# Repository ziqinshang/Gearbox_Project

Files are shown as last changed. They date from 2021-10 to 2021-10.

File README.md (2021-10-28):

# Gearbox_Project
### This is a group project of a gear reduction system, The system consist of three shafts: Input, Intermediate and Output Shaft, Two pinions and two gears, all helical, with a gear reduction ratio of 1:16. The shafts are supported by appropriate bearings, A outer shell were also constructed for convering the inner components.
#### All the mathmatical calculations were performed using MATLAB
#### The prototype were modelled using Solidworks
#### Detailed engineering drawing were generated by Solidworks
#### Some hand-drawn graphs are available on design report
##### Group Effort
##### credit: Mingyang Xu, Maiduo Wu

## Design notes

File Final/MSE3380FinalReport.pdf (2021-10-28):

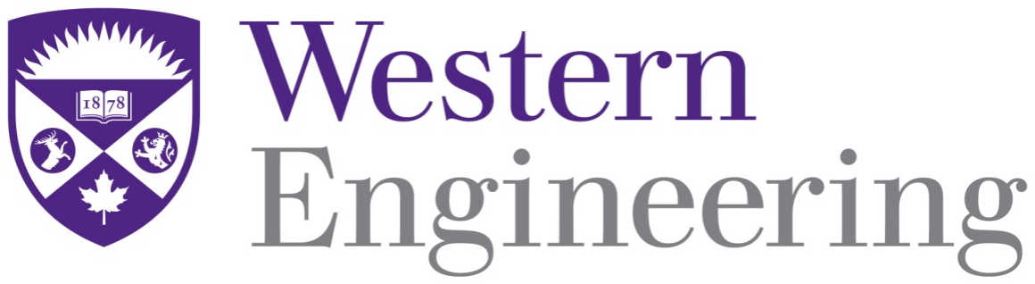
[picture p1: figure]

# MSE3380

## Mechanical Components Design for Mechatronic Systems Final Design Report

Group 5

Mingyang Xu (250902744)

Mai Duo Wu (250922745)

Ziqin Shang (250890594)

April 9th, 2019

Table of Contents

7. Bearing specification (manufacturer/model number) configuration and life calculation. Specify a

## Introduction

In the previous report, the gear specifications were determined, corresponding calculations

and CAD drawings were also completed. In this final report, the gearbox design will be

finalized, and results will be verified. a complete analysis of shaft and bearing, calculations

of shaft fatigue safety factor, shaft material endurance limit and bearing life will be

conducted.

## 1. Summary of The Analysis from The Phase 1 Report

Performance Specifications

In the interim report, the performance specification was firstly determined, including

the important specifications of weight, size and efficiency; constrains of gears, motor,

lifetime and output; and associated assumptions.

Gear Ratios and Reduction Stages

The gear ratio and reduction stages were specified, after a series of analysis including

DC motor no-load speed, DC motor stall torque and DC motor peak power, the required

torque output of DC motor was determined to be 3.717N.m, and the required speed output

was determined to be 9426rpm. Based on the calculated torque output, the gear ratio was

calculated to be 1:16.4, in order to implement this gear ratio, the two reduction stages were

determined to be 1:4 for both stages.

Torque Within the Shafts

The torque within the shaft was estimated, the shaft that connects to the DC motor will

experience least torque, which is the output of DC motor of 3.717N.m. And the

intermediate shaft will experience a torque of 14.105N.m, the final shaft will experience

most torque which is calculated to be 53.525N.m.

Forces on The Pinions and Gears and Their Dimensions

The forces on the pinions and gears and their dimensions was determined, the forces

between DC motor pinion and intermediate gear is calculated to be 2163.12N, the forces

between intermediate pinion and output gear is calculated to be 2052.14N. The gears were

carefully selected from the Boston gears catalog, the two pinions have the same dimensions

but different direction, with a transverse diametral pitch of 16 inch, 12 teeth, a pitch

diameter of 0.75 inch, a bore diameter of 0.375 inch, a keyway dimension of 1/16x1/32, A

style, and the catalog number is H1612R and H1612L respectively. The two gears also have

the same dimensions but different direction, with a transverse diametral pitch of 16 inch, 48

teeth, a pitch diameter of 3 inches, a bore diameter of 0.5 inch, a keyway dimension of

1/8x1/16, a style, and the catalog number is H1648R and H1648L respectively.

Contact and Bending Stress, Contact and Bending Safety for the Gears

The contact stress, bending stress, contact safety factor and bending safety factor of the

gears was calculated using MATLAB script, and the results is summarized below.

| Pinion 1 | Gear 2 | Pinion 3 | Gear 4
Bending Stress | 42209 | 40015 | 34607 | 33254
Contact Stress | 167743 | 94295 | 151888 | 85960

Bending FOS | 1.0 | 1.10 | 1.27 | 1.40
Contact FOS | 0.75 | 1.38 | 1.1 | 1.55

Additionally, the CAD model of the entire gearbox was completed, and the 2D assembly

drawing of the entire gearbox with cross-section was also drawn using Solidworks.

Updates

Due to fact that the calculated pinion 1 contact FOS is less than 1(Pinion 1 cannot

withstand such high pressure), all 4 gears’ transverse diametral pitch are changed to be 8 so

that the gear can withstand such a pressure and they can fit together without interference.

The specifications for newly updated gears can be found in appendix A.

## 2. Free Body Diagrams for Shafts

Included in Section 3: Calculation of All Torques and Forces Acting on Shafts

## 3. Calculation of All Torques and Forces Acting on Shafts

Firstly, the reaction forces in each shaft was determined, each shaft is supported by two

bearings that treated as a fixed support, since the helical gears are used, the forces between

the gear and pinion is three-dimensional, that is, force is acting on x, y and z axis. Detailed

calculations for reaction forces are demonstrated below.

Shaft 1 (Input Shaft):

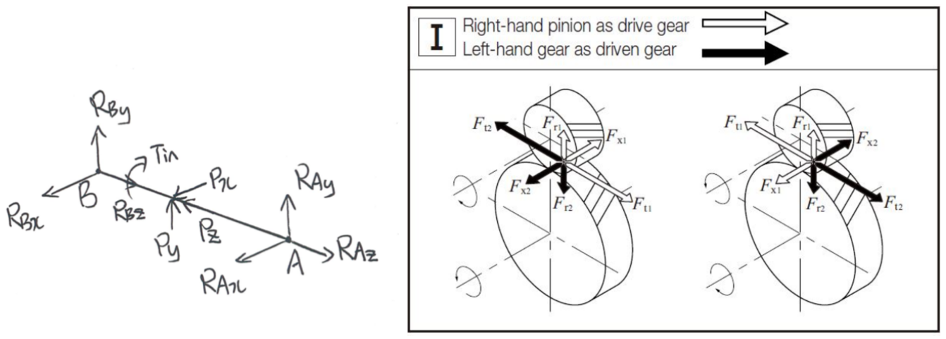
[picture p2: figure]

Figure 1. Free Body Diagram for input shaft

The forces between pinion 1 and gear 2 is calculated to be: P" = −W&'( = T

r = 14.105N. m
0.01905m = −740.42N

P5 = −W6'( = W&'( tanφ& = 740.42 ∗ tan 20.09 = −270.81N

P= = −W>'( = W&'( tan ψ = 740.42 ∗ tan 45 = −740.42N W = W&
cos ψ cosφC

= 740.42
cos 14.5 cos 45 = 1081.56N

From Free Body Diagram, the following equations can be listed:

ΣMG= = P=(1) + RL=(2) = 0

ΣMG5 = P5(1) + RL5(2) = 0

ΣF" = RL" + RG" − P" = 0 RG" = RL"(Assumption)

ΣF= = RL= + RG= + P= = 0

ΣF5 = RL5 + RG5 + P5 = 0

Solving equations above, the results are:

RL= = 370.21N | RL5 = 135.405N | RL" = −370.21N
RG= = 370.21N | RG5 = 135.405N | RG" = −370.21N

Shaft 2 (Intermediate Shaft):

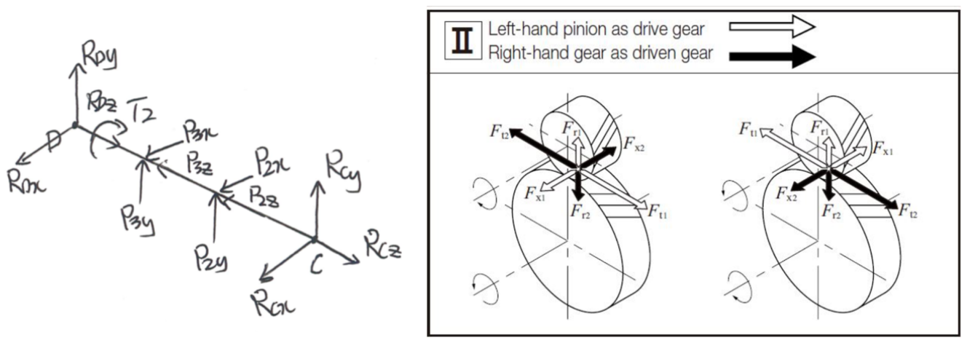
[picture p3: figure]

Figure 2. Free Body Diagram for intermediate shaft

The distance between point D and point 3 is determined to be 1/6 of the total shaft

length, distance between point 3 and shaft midpoint is determined to be 2/6 of the total

shaft length. The shaft is symmetrical.

The forces between pinion 3 and gear 4 and pinion 1 and gear 2 can be calculated based on

previous given formulas:

P(" = W&'( = P

6 = 'Q.'RST.U
R.R'VRSU = 740.42Ne

P(5 = W6'( = W&'( tanφ& = 740.42 ∗ tan 20.09 = 270.81N

P(= = W>'( = W&'( tan ψ = 740.42 ∗ tan 45 = 740.42N PW" = W&WQ = T

r = 53.525N. m
0.0762m = 702.43N

PW5 = W6WQ = W&WQ tanφ& = 1404.86 ∗ tan 20.09 = 256.9N

PW= = W>WQ = W&WQ tan ψ = 1404.86 ∗ tan 45 = 702.43N W = W&
cos ψ cosφC

= 702.43
cos 14.5 cos 45 = 1026.07N

From Free Body Diagram, the following equations can be listed:

ΣMX5 = PW5(1) + P(5(5) + RY5(6) = 0

ΣMX= = PW=(1) + P(=(5) + RY=(6) = 0

ΣF" = RX" + RY" + PW" − P(" = 0 RY" = RX"(Assumption)

ΣF5 = RY5 + RX5 + P(5 + PW5 = 0

ΣF= = RY= + RX= + P(=+ PW= = 0

Solving equations above, the results are:

RY= = −734.09N | RY5 = −268.492N | RY" = −19N
RX= = −708.76N | RX5 = −259.218N | RX" = −19N

Shaft 3 (Output Shaft):

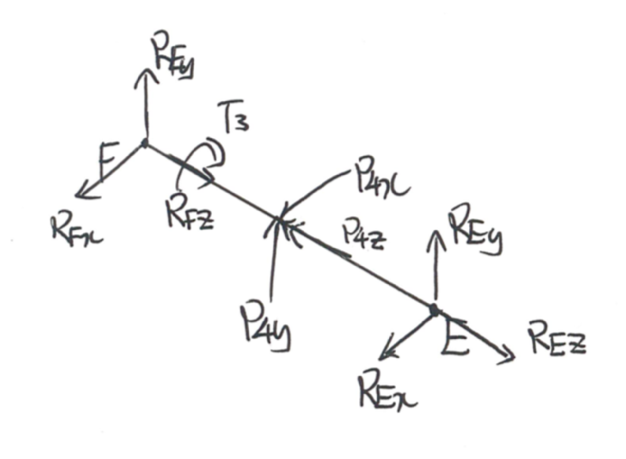
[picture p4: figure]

Figure 3. Free Body Diagram for output shaft The forces between pinion 3 and gear 4 can be calculated based on previous given formulas: PQ" = −W&WQ = T

r = 53.525N. m
0.0762m = −702.43N

PQ5 = −W6WQ = W&WQ tanφ& = 1404.86 ∗ tan 20.09 = −256.9N

PQ= = −W>WQ = W&WQ tan ψ = 1404.86 ∗ tan 45 = −702.43N

From Free Body Diagram, the following equations can be listed:

ΣMZ= = PQ=(1) + R[=(2) = 0

ΣMZ5 = PQ5(1) + R[5(2) = 0

ΣF" = RZ" + R[" − PQ" = 0 RZ" = R["(Assumption)

ΣF= = RZ= + R[= + PQ= = 0

ΣF5 = RZ5 + RZ5 + PQ5 = 0

Solving equations above, the results are:

R[= = 351.22N | R[5 = 128.46N | R[" = −351.22N
RZ= = 351.22N | RZ5 = 128.46N | RZ" = −351.22N

## 4. Shear, Moment and Torque Diagrams for Shafts

Pictures on next page.

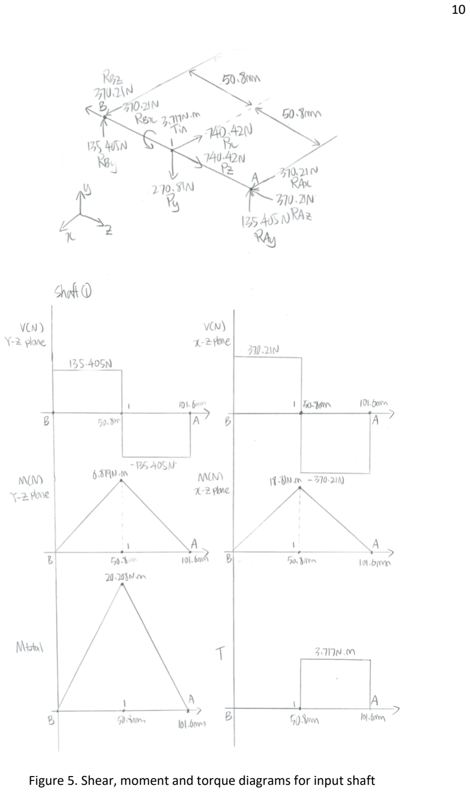
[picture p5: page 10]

Figure 5. Shear, moment and torque diagrams for input shaft

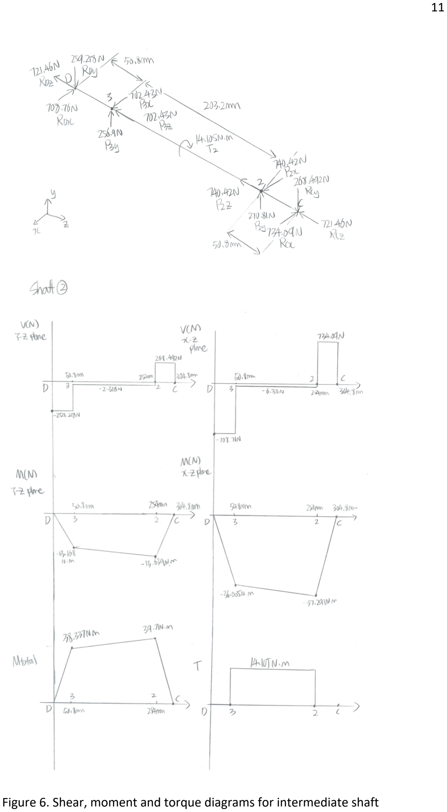
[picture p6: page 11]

Figure 6. Shear, moment and torque diagrams for intermediate shaft

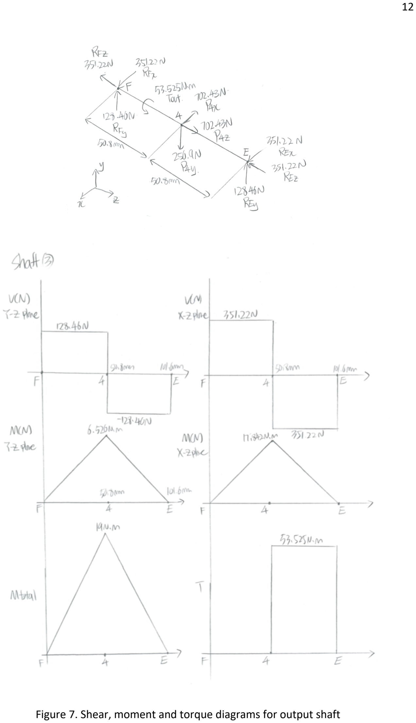
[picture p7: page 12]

Figure 7. Shear, moment and torque diagrams for output shaft

## 5. Fully Corrected Endurance Limit for Shaft Material

Include in Section 6. Shaft Fatigue Safety Factors

## 6. Shaft Fatigue Safety Factors

To obtain the endurance limit for shaft material, the shaft material needs to be determined,

the yield strength and tensile strength of the material needs to be sufficient in order to

prevent failure. In the case of transmission shaft, the material with high torsional rigidity

and fatigue resistance is preferred, which are steel and aluminum. Steel is extremely

durable, inexpensive, but heavy. On the other hand, aluminum is less durable but

significantly more lightweight than steel. In this application, lightweight is not a major

requirement, but high strength is preferred, as a result, steel is chosen for this application.

For initial test, AISI 1060 was implemented to calculate the endurance limit.

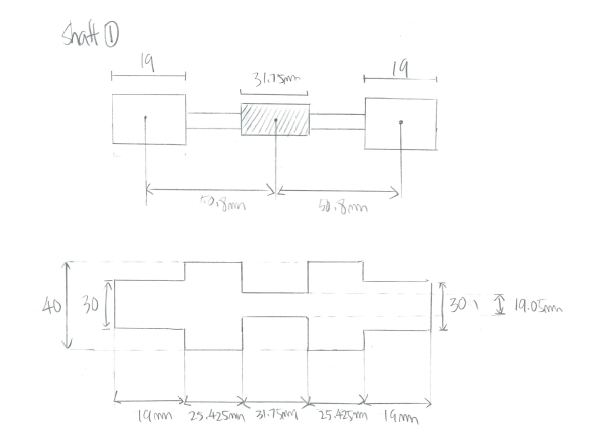
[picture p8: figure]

Figure 8. Dimensions for input shaft

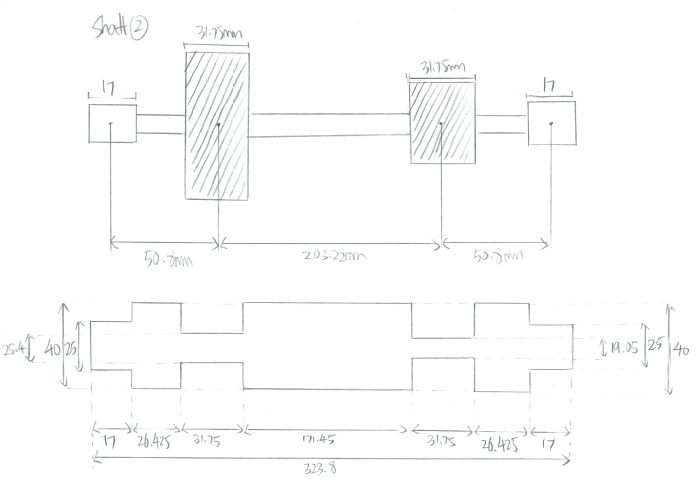
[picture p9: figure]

Figure 9. Dimensions for intermediate shaft

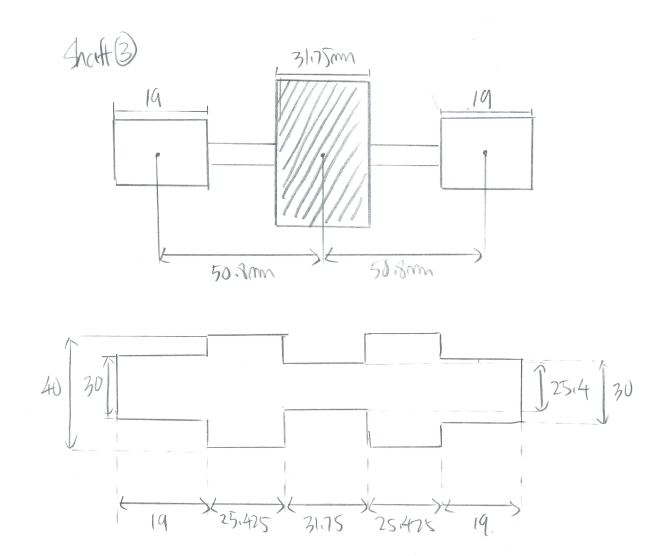
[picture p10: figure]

Figure 10. Dimensions for output shaft In order to determine endurance limit, the following analysis is performed.

1. The rotary-beam test specimen endurance limit of AISI is determined to be 340 MPa.

Using the equation

s]

^ = _

0.5Sa& Sa& ≤ 200kpsi (1400 MPa)
100 kpsi | Sa& > 200kpsi
700 MPa | Sa& > 1400 Mpa

As the Sut, the tensile strength of AISI 1060 is 680MPa, which is smaller than 1400 MPa,

the rotary-beam test specimen endurance is half of the tensile strength which is 340

MPa.

2. The corrected endurance limit at the critical location of a machine part in the

geometry and condition of use is given as:

S] = k>khkikjk]kkS]

^

The surface condition modification factor is given as k> = aSa&

h , where a and b are

found using the following table:

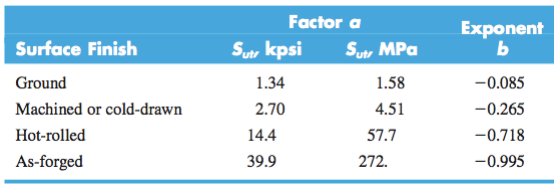
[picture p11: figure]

Solving the equation using the parameters of Machined or cold-drawn assuming the

shaft should be machined, ka = 0.8009.

3. The size factor is evaluated using the equations

The size factor is determined to be 0.9046 for shaft 1 and 2, and 0.8772 for shaft 3.

4. The Loading Factor Kc is determined to be 1 as the load factor is bending.
5. The temperature factor Kd is determined to be 1 as the electric drill should be used

in a room temperature condition.

6. The reliability factor, Ke was determined using the following table

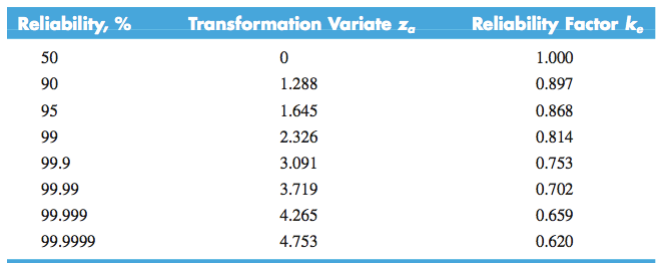
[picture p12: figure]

With 99% reliability, Ke was determined to be 0.814.

7. Miscellaneous-effects factor kf is assumed to be 1.

Then, fatigue stress-concentration factor is solved using the equation:

Kk = 1 +

K& − 1
1 + ma/r

Where Kt is the stress-concentration factor, a is the√a is the Neuber constant and r

is the fillet radius. Please see MATLAB files for calculations.

The stress is calculated using σ6]q = ri
s

.M is the moment derived from moment

diagram where stress concentration is located at the fillet transition location. c is the

radius of the smaller part of the shaft, and I is solved from I = ujv
wQ

. Refer to MATLAB for

calculations

The fatigue safety factors for shafts is solved as nk = Endurance limit Maximum reverseal stresses nk = S] Kkσ6]q

The results obtained are listed below:

| Se | Kf | srev | nf
Shaft 1 | 200.5MPa | 1.4811 | 26.04MPa | 5.20
Shaft 2 | 200.5MPa | 1.4811 | 58.17MPa | 2.33
Shaft 3 | 104.4MPa | 1.6077 | 24.5MPa | 4.93

All three shafts have a fatigue safety factors greater than 1 with a reliability of 99%. This

shows that the shafts should have an infinite life. This result is reasonable as the used

material for the shaft is steel which has a high tensile strength.

## 7. Bearing specification (manufacturer/model number) configuration

and life calculation. Specify a recommended lubrication strategy.

Firstly, the bearing type needs to be determined, in this application, helical gears were

used, as a result, there are thrust load and radial load exist. Bearings are manufactured to

take pure radial loads, pure thrust load or the combination of two, ball bearings are

considered to be the most suitable type for this application due to the fact that ball bearing

can withstand both thrust load and radial load in a considerable amount. Specifically, single-

row deep groove ball bearing was decided to be implement, since single-row deep groove

ball bearing is excellent for high-speed application, has good radial load capacity and

satisfactory thrust load capacity in both directions, and low torque capacity at start-up and

running speed. All bearings are selected from The Timken Company.

To further specify the bearing specification, the dynamic load and static load needs to

be determined, following procedures were used to determine these two values. Assuming:

- Continuous one-shift operation at 9426 rpm (8 hours day, 5-day week),

life=30kh

- Commercial gear, load factor = 1.2
- 90% reliability
- a=3 for ball bearing

Shaft 1:

Estimate life for 8-hour day:

LX = 9426rpm × 30kℎ ×

60m
ℎ = 1.6967 × 10'Rrev

The equivalent load:

F] = XÜVF6 + YÜF> , V = 1

Radial load = 394.2N Axial load = 370.12N

Since
F>

(VF6) = 370.21
394.2 = 0.939 > e eU>= = 0.44

Thus

F] = X((394.2) + Y((370.21)

First guess: X( = 0.56 Y( = 1.63

F] = 0.56(394.2) + 1.63(370.21) = 824.19N

Weibull parameters

xR = 0.02 θ = 4.459 b = 1.483

From Eq. (11–10):

C'R = 1.2(824.19) ç
é

1.6967 × 10'R
10w è

0.02 + (4.459 − 0.02)(1 − 0.90)

'

'.QêWë

'
W
= 25414.23N = 25.41kN

From T 11–2 (DG) bearing 02-40 mm has

C'R = 30.7kN CR = 16.6kN
F>
CR

= 0.0223, e ≈ 0.21, Y( = 2.15

F] = 0.56(394.2) + 2.15(370.21) = 1016.7N

C'R = 1.2(1016.7) ì

1.6967 × 10'R
10w î

'
W
= 31.35kN

From T 11–2 (DG) bearing 02-45 mm has

C'R = 33.2kN CR = 18.6kN
F>
CR

= 0.0199, e ≈ 0.2069, Y( = 2.1736

F] = 0.56(394.2) + 2.1736(370.21) = 1025.43N

C'R = 1.2(1025.43) ì

1.6967 × 10'R
10w î

'
W
= 31.62kN

Selecting from The Timken Company ball bearings catalog, two 30mm bore single-row deep

groove ball bearing will be used in both ends of input shaft. The bearing has a outside

diameter of 72mm, a width of 19mm, a fillet radius of 1.0mm, a weight of 0.354kg, a static

load rating of 15600N and an extended dynamic load rating of 33900N.

Bearing life:

ℒ'R = 60ℒñnñ
60nX

(

C'R
F]

)> = 10w
60(9426rpm)

## é ³³⁹⁰⁰

1025.43è

W
= 63885.5ℎ

Shaft 2:

Point C: Radial load = 781.65N Axial load = 19N F>

(VF6) = 19N
781.65N = 0.02431 < e eUÜC = 0.19

F] = 1(781.65) + 0(19) = 781.65N

C'R = 1.2(781.65) ì

1.6967 × 10'R
10w î

'
W
= 24.10kN

Point D: Radial load = 754.68N Axial load = 19N F>

(VF6) = 19N
754.68N = 0.02517 < e eUÜC = 0.19

F] = 1(754.68) + 0(19) = 754.68N

C'R = 1.2(754.68) ì

1.6967 × 10'R
10w î

'
W
= 23.27kN

Since the e is minimum for both bearings, no iteration needs to be performed, Selecting

from The Timken Company ball bearings catalog, two 25mm bore single-row deep groove

ball bearing will be used in point C and D of intermediate shaft. The bearing has a outside

diameter of 62mm, a width of 17mm, a fillet radius of 1.0mm, a weight of 0.236kg, a static

load rating of 12200N and an extended dynamic load rating of 26600N.

Bearing life at Point C:

ℒ'R = 60ℒñnñ
60nX

(

C'R
F]

)> = 10w
60(2356.5rpm)

é

26600
781.65è

W
= 278733.5ℎ

Bearing life at Point D:

ℒ'R = 60ℒñnñ
60nX

(

C'R
F]

)> = 10w
60(2356.5rpm)

é

26600
754.68è

W
= 309697.5ℎ

Shaft 3:

Radial load = 373.98N Axial load = 351.22N F>

(VF6) = 351.22N
373.98N = 0.939 > e eU>= = 0.44

F] = X((373.98) + Y((351.22)

First guess: X( = 0.56 Y( = 1.63

F] = 0.56(373.98) + 1.63(351.22) = 781.92N

Weibull parameters

xR = 0.02 θ = 4.459 b = 1.483

From Eq. (11–10):

C'R = 1.2(781.92) ì

1.6967 × 10'R
10w î

'
W
= 24.11kN

From T 11–2 (DG) bearing 02-35 mm has

C'R = 25.5kN CR = 13.7kN
F>
CR

= 0.0256, e ≈ 0.215, Y( = 2.07

F] = 0.56(373.98) + 2.07(351.22) = 936.45N

C'R = 1.2(936.45) ì

1.6967 × 10'R
10w î

'
W
= 28.88kN

From T 11–2 (DG) bearing 02-40 mm has

C'R = 30.7kN CR = 16.6kN
F>
CR

= 0.0212, e ≈ 0.21, Y( = 2.15

F] = 0.56(373.98) + 2.15(351.22) = 964.55N

C'R = 1.2(964.55) ì

1.6967 × 10'R
10w î

'
W
= 29.74kN

Selecting from The Timken Company ball bearings catalog, two 30mm bore single-row deep

groove ball bearing will be used in both ends of input shaft. The bearing has a outside

diameter of 72mm, a width of 19mm, a fillet radius of 1.0mm, a weight of 0.354kg, a static

load rating of 15600N and an extended dynamic load rating of 33900N.

Bearing life:

ℒ'R = 60ℒñnñ
60nX

(

C'R
F]

)> = 10w
60(589rpm)

é

33900
964.55è

W
= 1228452ℎ

For this application, oil is a preferred lubricant because the rotational speed is very high, at

high speed, non-viscous lubricant is required to achieve less start up and running torque and

have higher speed capability, and grease is not suitable for this application because it generates much higher amount of rolling resistance than oils. However, oil have much high

evaporation rate than grease, thus the bearing needs to be maintained frequently.

The bearings specifications are summarized in Appendix A, note that all bearings are

single-row deep groove ball bearing that selected from The Timken Company.

## Conclusion

By using the appropriate specifications and criteria, the appropriate shafts, bearing and

gears were identified. Using AISI 1060 and the parameters according to the graphs shown in

the previous sections, the factor of safety of all shafts are above one, which indicate that the

shafts should have an infinite life. Thus, the failure of shafts would not be likely to occur.

The bearings are found to have a minimum bearing life of 63886 hours, which is much larger

than the desired life of 4000 hours according to the requirements of the project

descriptions. By using these shafts and bearing, these would satisfy the task proposed by the

project guideline.

## References

R. G. Budynas and J. K. Nisbett. Shigley’s Mechanical Engineering Design, New York, NY:

McGraw-Hill Education, 2015

Timken, “Deep Goove Ball Bearings,” Timken Deep Groove Ball Bearing Catalog, 2017

## Appendix A. Specification Sheets

Important Note: In the submitted CAD drawings, the bearing 306K are

replaced with 305K since the 306K CAD drawing cannot be found.
| Bore (mm) | Outside Diameter (mm) | Width (mm) | Fillet Radius (mm) | Weight (kg) | Static Load Rating (N) | Extended Dynamic Load Rating(N) | Catalog Number
Bearing A | 30 | 72 | 19 | 1 | 0.365 | 15600 | 33900 | 306K
Bearing B | 30 | 72 | 19 | 1 | 0.365 | 15600 | 33900 | 306K
Bearing C | 25 | 62 | 17 | 1 | 0.236 | 12200 | 26600 | 305K
Bearing D | 25 | 62 | 17 | 1 | 0.236 | 12200 | 26600 | 305K
Bearing E | 30 | 72 | 19 | 1 | 0.365 | 15600 | 33900 | 306K
Bearing F | 30 | 72 | 19 | 1 | 0.365 | 15600 | 33900 | 306K

Table 1. Bearing specifications

| Transvers e Diametral Pitch | Numbe r of Teeth | Pitch Diamete r | Bore | Keyway | Style | Hub Dia. | Hub Proj. | Overall length | Direc tion | Catalog Number
Pinion 1 | 8 | 12 | 1.5 | 0.75 0 | 3/16x3/3 2 | A | 1.25 | 0.50 | 1.25 | Right Hand | HS812R

Gear 2 | 8 | 48 | 6.0 | 1.0 | 1/4x1/8 | B | 2.25 | 0.50 | 1.25 | Left Hand | HS848L
Pinion 3 | 8 | 12 | 1.6 | 0.75 0 | 3/16x3/3 2 | A | 1.25 | 0.50 | 1.25 | Left Hand | HS812L
Gear 4 | 8 | 48 | 6.0 | 1.0 | 1/4x1/8 | B | 2.25 | 0.50 | 1.25 | Right Hand | HS848R

Table 2. Updated Gear specifications

Component | Material
Bearing A | Steel
Bearing B | Steel
Bearing C | Steel
Bearing D | Steel
Bearing E | Steel
Bearing F | Steel
Pinion 1 | Steel–Hardened
Gear 2 | Steel–Hardened
Pinion 3 | Steel–Hardened
Gear 4 | Steel–Hardened
Input Shaft | AISI 1060
Intermediate Shaft | AISI 1060
Output Shaft | AISI 1060
Gearbox Housing | AISI 1060

Table 3. Components material specifications

## Appendix B. Detailed and Assembly Drawings

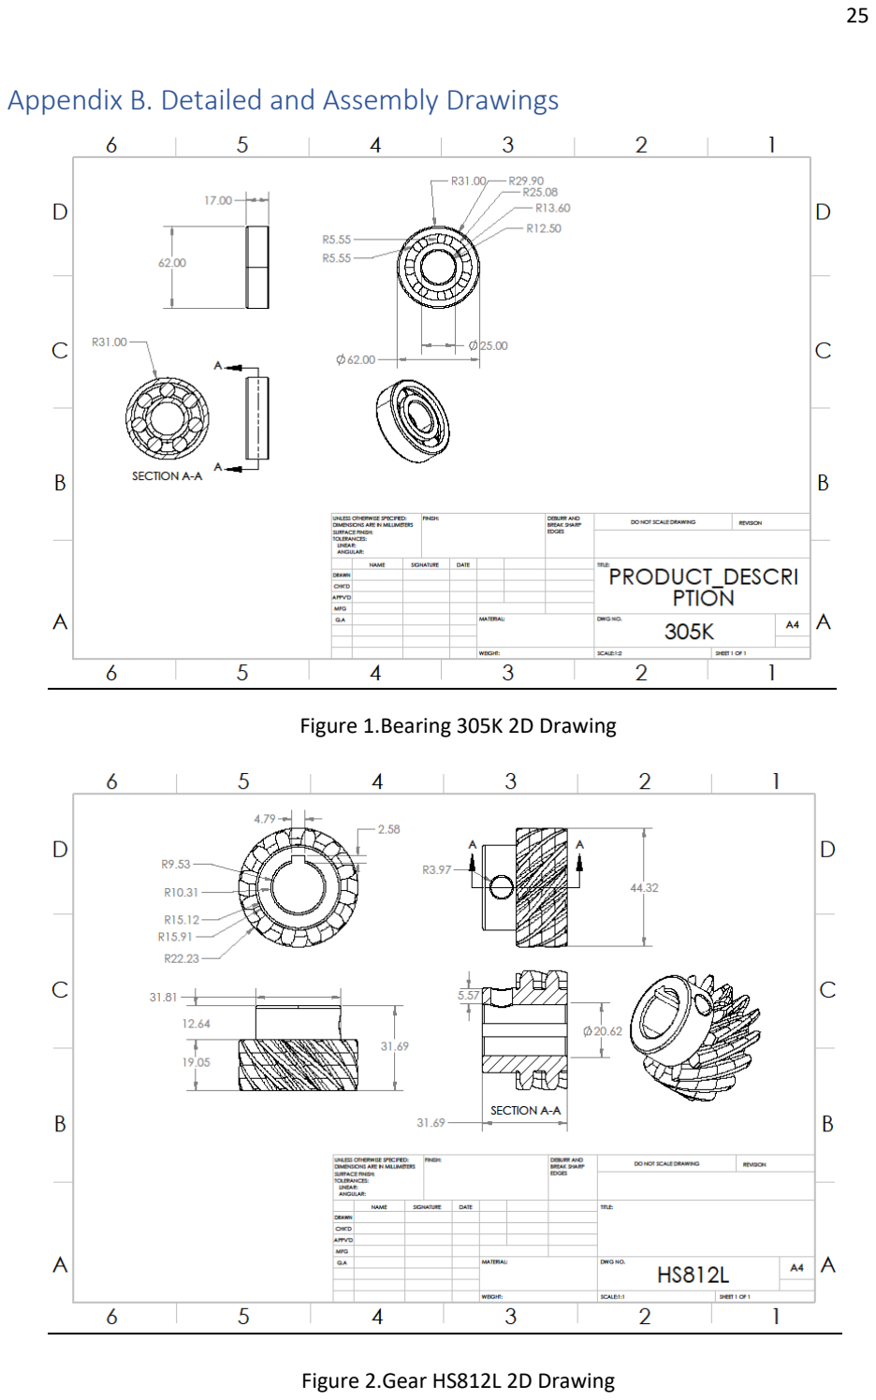
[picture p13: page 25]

Figure 1.Bearing 305K 2D Drawing

Figure 2.Gear HS812L 2D Drawing

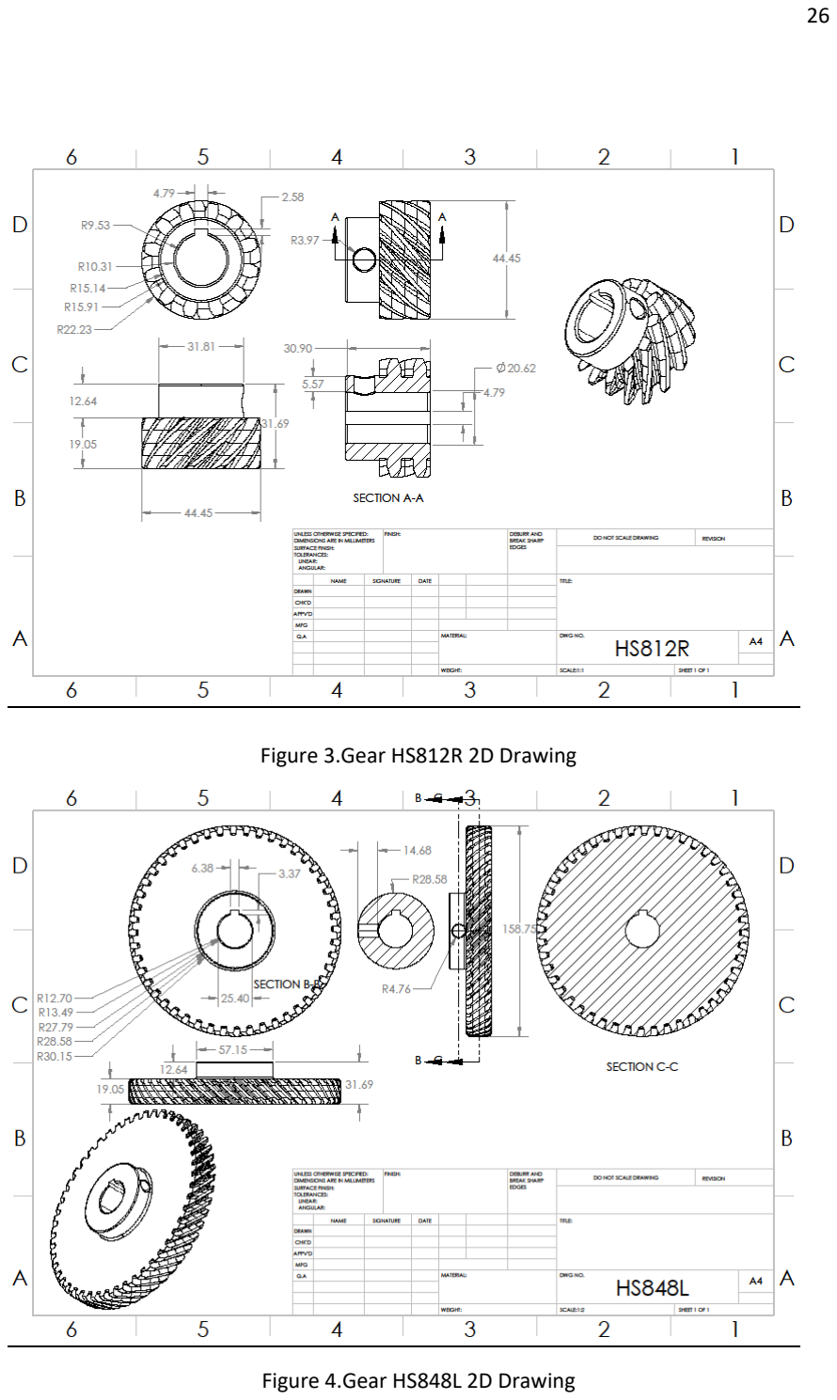
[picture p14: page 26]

Figure 3.Gear HS812R 2D Drawing

Figure 4.Gear HS848L 2D Drawing

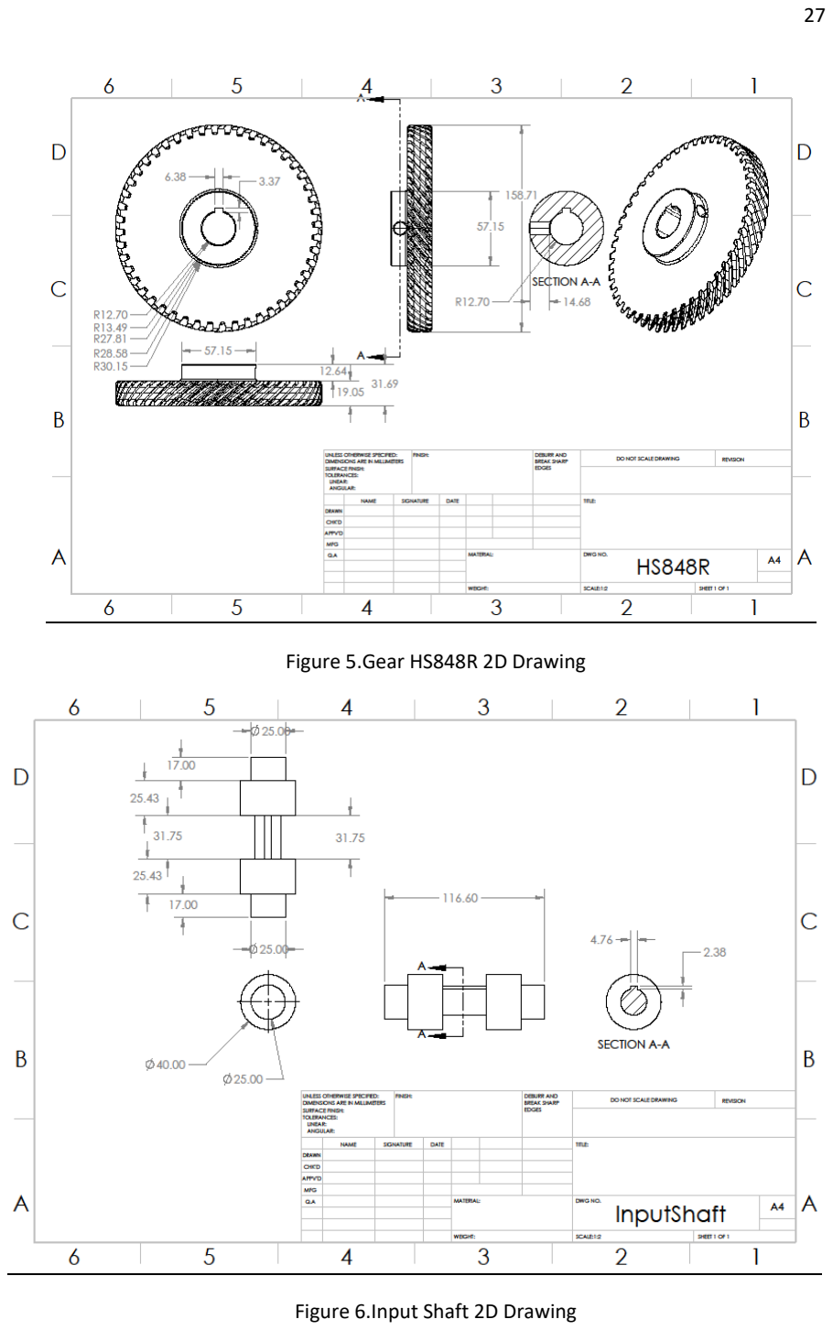
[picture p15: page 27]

Figure 5.Gear HS848R 2D Drawing

Figure 6.Input Shaft 2D Drawing

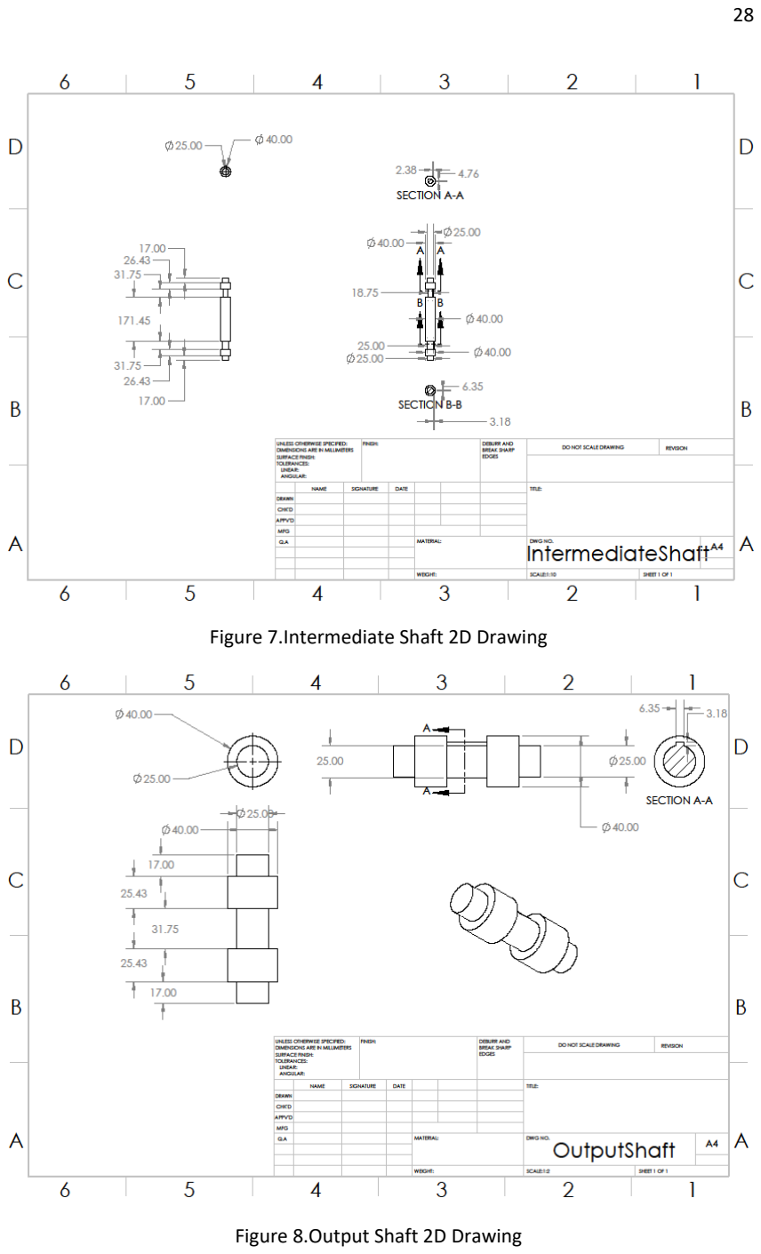
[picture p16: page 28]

Figure 7.Intermediate Shaft 2D Drawing

Figure 8.Output Shaft 2D Drawing

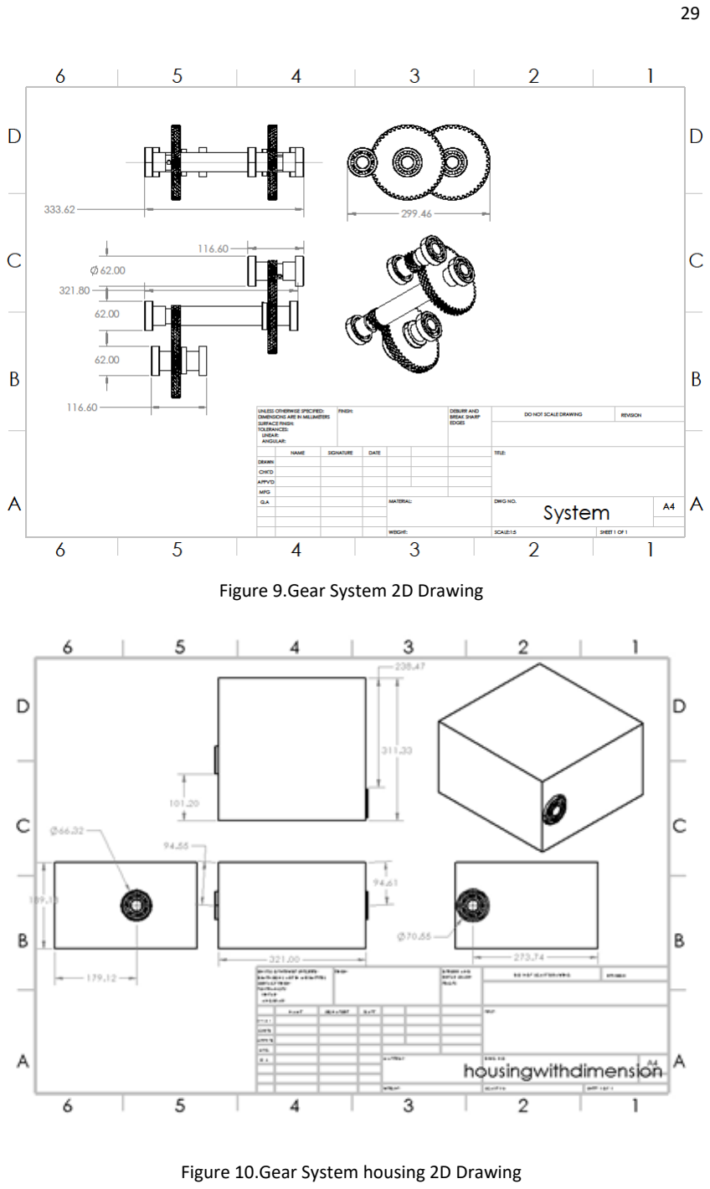
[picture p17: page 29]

Figure 9.Gear System 2D Drawing

Figure 10.Gear System housing 2D Drawing

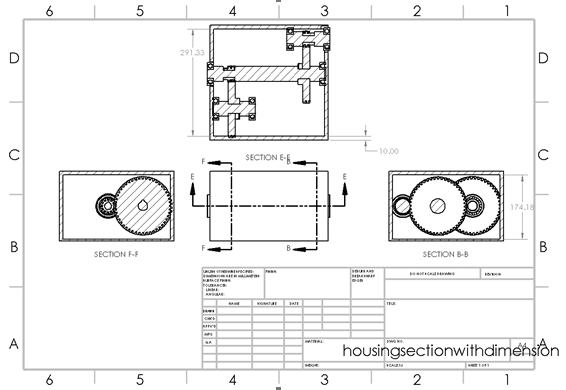
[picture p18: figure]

Figure 11. Gear System housing sectional view 2D Drawing

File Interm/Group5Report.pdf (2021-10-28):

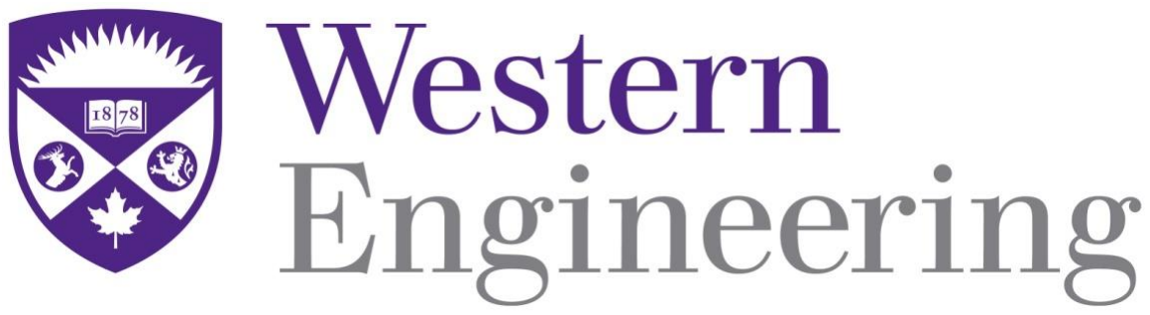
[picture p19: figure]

## Mechanical Components Design for Mechatronic Systems

## Design Project Report

Design Project Team 5

Mingyang Xu

Maiduo Wu

Ziqin Shang

## Table of Content:

Introduction Page 1

Performance Specification Page 1

-Objectives Page 1

-Constraints Page 2

-Assumptions Page 2

Gear Specification Page 3

-Motor Analysis Page 3

-Gear Analysis Page 5

-Gear Ratio Page 5

-Gear Interference page 6

-Gear Selection page 6

-Gearbox Design Page 8

Estimation of torque within shaft Page 9

Force on the gears Page 10

Stress Analysis Page 11

Discussion Page 15

Appendix

Citation

## Introduction

The primary goal for the design project is to create a transmission system for a single-

speed electric drill. This tool is designed to be used in heavy-duty applications such as mining

with long time continuous usage.

The goal for this specific report is designing suitable gears set that meets all the

performance specifications and constraints of the described electric drill.

## Performance Specifications

### Objectives

Based on the project descriptions, the following objectives are obtained in order to

design a suitable gearbox:

- Size: The size of the gearbox should not exceed the dimension of the existing motor,

which has an overall length of 88.9mm and a diameter of 46.831mm.

- Weight: Due to the fact that the drill is supposed to be operate by hand, the weight of

the gearbox should be minimized.

- Cost: Since the drill is a commercial product, the related manufacturing expenditure

should be minimized in order to keep a competitive price.

- Efficiency: The efficiency of the gearbox should be maximized in order to minimize

energy loss during the transmission process and reduce the energy consumption.

These objectives are only applicable for the gears of drill. Different objectives for shaft, bearing, components connections, fasteners and housing will be generated in the final report.

### Constraints

- Motor: The motor has a nominal operating voltage of 40 VDC, a torque constant of

8.474 N.mm/A and a voltage constant of 1125 rpm/V, the input pinion will be mounted

on the output shaft of the motor.

- Gears: For this design project, the spur gear and helical gear are the only two available

choices, the pressure angles are limited to be 14.5 or 20 degrees, the gear system design

is required to be a two-stage reduction, all gears have to be selected from Boston gear

catalog.

- Lifetime: The drill is designed to have a duty requirement of 8 hours a day, 5 days a week,

for 50 weeks in the year, which is 3200 hours per year, the drill has a minimum warranty

of 2 years, which means the drill has to last 6400 hours in operation.

- Output: the output torque for the drill is required to be 55 N.m, and the output speed of

575 rpm, to meet this requirement, the gear ratio will be implemented.

### Assumptions

The following assumption has been given in the design specification:

- A gearing efficiency of 90%, each reduction stage has a gearing efficiency of 94.87%.
- Neglect any limits on the current the battery is able to provide
- The associated heat generated is adequately dissipated by the cooling fan mounted on

the rotor

- The input pinion of the gearbox will be integral to the rotor of the electric motor

## Gear Specification

### Motor Analysis

Given specifications:

- Torque constant: 8.474 × 10⁽⁾ N ∙ m/A
- Voltage constant: 1125rpm/V
- No-load current: 2.6A
- Armature resistance: 0.072oℎm
- Voltage: 40V
- Back EMF constant: K9 = ; <=>?@A9 B=CD@?C@ = 8.89e − 4 V/rpm

Assumptions:

- Speed and torque have linear relationship
- Current and torque have linear relationship
- The motor is modelled as general DC Brush/Brushless motor

Mathematic Model of the DC motor:

V= = (I × R) + V9

V= = (I × R) + ω × K9

V= = N

T
K@

× RP + ω × K9

- No-load speed:

40V = (2.6A × 0.072Ω) + ω × 8.89e − 4 V/rpm

ω = 44789.4 rpm

- Stall torque:

40V = I × 0.072oℎm

I = 555.6A

TD@?>> = I × K@ = 4.708 N ∙ m

The peak power occurred at half way of the speed torque graph. The speed and torque

relationship of this motor is ω = −9513.5T + 44789.4 , At peak power, the torque is

2.354 N ∙ m, speed is 22395 rpm. The peak power can be calculated as

PT9?U = T ∙ ω = 2 ∙ π ∙ W

nYTZ
60 [ ∙ T = 5520W

Considering the 90% gear efficiency, the peak output power is then 4968W. The required

output torque is 55 N ∙ m and the required output speed is 575 rpm. Therefore, the required

output power is 3.31KW. The motor is able to product the output power. In order to archive the

required power, the motor will be running at less than peak power.

The required output of the motor: ] A9?Y 9^^B_9CB` = ⁾.);Ua
bc% = 3678W
| H = T × ω × 0.105

3678W = T × (−9513.5T + 44789.4) × 0.105

T = 3.717N ∙ m or 0.99N ∙ m

At T = 3.717N ∙ m, the speed is 9428 rpm, the required gear ratio is 16.4

At T = 0.99N ∙ m, the speed is 35371 rpm, the required gear ratio is 61.7

The smaller gear ratio is generally more preferred and more likely to have inertia matching;

therefore, motor is set to be running at torque = 3.717N ∙ m, speed = 9426 rpm.

### Gear Analysis

Gear Ratio

As recommended by American Gear Manufactures Association (AGMA), gear ratio of

each pair is advised to be less than 1:8. After going through the Spur and Helical sections of

the Boston gear sheet, the closet combined gear ratio is 16. This gear ratio can be achieved by

using a compound gear train, a 1:4 pair followed by another 1:4 pair.

The exact gear ratio of 16.4 cannot be achieved exactly, with the gear ratio of 16

implemented, the output torque is slightly lower than required (The output torque is 53.6 N ∙

m, 2.5% less).

The exact torque and speed output cannot be achieved using this specified gear ratio 16 as

the torque and speed curve does not cross this output point. To achieve the exact output, PWM

voltage control needs to be implemented to adjust the voltage for the torque and speed curve

to cross the exact point.

In the following discussion, only gearbox with 16 gear ratios is implemented, PWM

voltage control is not implemented. The primary reason for allowing this slight variance in

torque and speed output is that this mathematic modelling is only an approximation, the 2.5%

difference introduced by the gearbox is acceptable.

Gear Interference

As instructed on the textbook, gear inference needs to be avoided at all cost. To avoid gear

interference, the smallest number of teeth on pinion and largest number of teeth on the larger

gear is calculated. Standard full teeth are used.

Spur gear selection

K=1

Gear ratio m=4

Normal pressure angle ∅ = 20 degree

Minimal number of required teeth on pinion:

NT = 2k (1 + 2m)sint∅ (m + umt + (1 + 2m)sint∅)

NT = 15.4 teetℎ

Therefore, the smallest number of teeth on the pinion needs to be at least 16 teeth to avoid

interference.

Maximum number of allowed teeth on larger gear:

N? = NT

tsint∅ − 4kt
4k − 2NTsint∅

N? = 101.4 teetℎ

Therefore, the largest number of teeth on the larger gear needs to be less than 101 teeth to avoid

interference with 16 teeth pinion.

The following gear sets are selected for Spur gear speed reducer:

Pair | Teeth | Pitch Diameter | Diametral Pitch | Datasheet page
1 | 16 | 0.500 | 32 | 39
1 | 64 | 2.000 | 32 | 39
2 | 16 | 1.000 | 16 | 43
2 | 64 | 4.000 | 16 | 43

### Helical gear selection

Normal pressure angle ∅w = 14.5 degree

Helix angle ∅x = 45 degree

Gear ratio m=4, K=1

Tangential pressure angle: ∅@ = tan⁽; (tan∅C)
cos∅
∅@ = 20.1°

Minimal number of required teeth on pinion:

NT = | 2kcosψ (1 + 2m)sint∅ (m + umt + (1 + 2m)sint∅)
| NT = 10.8 teetℎ

Therefore, the smallest number of teeth on the pinion needs to be at least 11 teeth to avoid

interference.

Maximum number of allowed teeth on larger gear:

N} = NT

tsint∅@ − 4ktcostψ
4kcosψ − 2NTsint∅@
N} = 14.99
−0.00357
The denominator being a very small negative number is due to numerical calculation

rounding, N} in this case is approaching positive infinity.

The following gear is selected for helical speed reducer:

Pair | Teeth | Pitch Diameter | Diametral Pitch | Datasheet page
1 | 12 | 0.750 | 16 | 64
1 | 48 | 3.000 | 16 | 64
2 | 12 | 0.750 | 16 | 64
2 | 48 | 3.000 | 16 | 64

Gear Box Design

Two configurations of gear choice are listed above, the chosen configuration of gearbox design

is Helical Gear. Helical gears are favored because helical gear offers smoother power

transmission and more compact size than Spur gear.

Parallel configuration of helical gear is chosen against crossed configuration for its higher

efficiency and reduced thrust load.

The final design of gear box is presented below:

Pair | Teeth | Pitch Diameter | Diametral Pitch | Datasheet page
1 | 12 | 0.750 | 16 | 64
1 | 48 | 3.000 | 16 | 64
2 | 12 | 0.750 | 16 | 64
2 | 48 | 3.000 | 16 | 64

## Estimation of the torque within the shafts

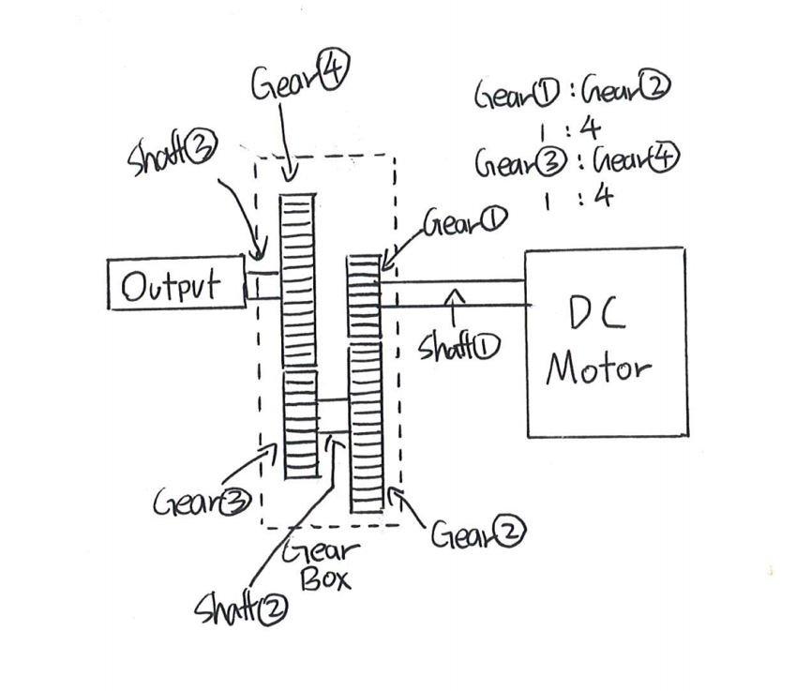
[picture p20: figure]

Based on the graph above, shaft 1 will experience least torque and shaft 3 will experience

most torque, the gear ratio between gear 1 and gear 2, gear 3 and gear 4 are both 1:4. Thus, the

torque exerted by DC motor is the torque that shaft 1 will experience, which is 3.717N.m.

TD?^@; = TÄÅZ=@=Y = 3.717N. m

As stated in assumption, with a gearing efficiency of 90%, each pair of gears will have a

efficiency of 94.87%, which is the square root of 90%, the torque within shaft 2 can then be

calculated as:

TD?^@t = μY9ÉÑB@_=C; ∗ 4 ∗ TD?^@; = 0.9487 ∗ 4 ∗ 3.717N. m = 14.105N. m

Similarly, the torque within shaft 3, which is the output torque can also calculate as:

TD?^@) = μY9ÉÑB@_=Ct ∗ 4 ∗ TD?^@t = 0.9487 ∗ 4 ∗ 14.105 = 53.525N. m

## The forces on the pinions and gears and their dimensions

Based on calculations made in part 2, a gear ratio of 16.4:1 was determined, to evenly

distribute this gear ratio to two reduction stages, both reduction stage implemented a 12 teeth

pinion and a 48 teeth gear in order to achieve a gear ratio of 1:4. After searching the Boston

Gears catalog, a pinion with 16 inch transverse diametral pitch, 12 teeth, 0.75 pitch diameter,

0.375 bore, 1/16 x 1/32 keyway, A style, right hand with a catalog number of H1612R was

determined, the dimension for following 3 gears and pinion was determined in a similar way,

the specific dimensions for each gears and pinions can be found in the table below:

| Transverse Diametral Pitch | Number of Teeth | Pitch Diameter | Bore | Keyway | Style | Direction | Catalog Number
Pinion 1 | 16 | 12 | 0.75 | 0.375 | 1/16x1/32 | A | Right Hand | H1612R
Gear 2 | 16 | 48 | 3.0 | 0.5 | 1/8x1/16 | A | Left Hand | H1648L
Pinion 3 | 16 | 12 | 0.75 | 0.375 | 1/16x1/32 | A | Left Hand | H1612L
Gear 4 | 16 | 48 | 3.0 | 0.5 | 1/8x1/16 | A | Right Hand | H1648R

A series of force analysis was implemented, the force on the pinions and gears was then

obtained, using the formula provided on 13-40, page 705, Shigley’s Mechanical Engineering

Design:
W@ = T
r

WY = W@ tanφ@

W? = W@ tan ψ
W = W@
cos ψ cosφC

Converting inches to meters:

0.75 incℎ = 0.01905m

3.00 incℎ = 0.0762m

The forces between pinion 1 and gear 2 can be calculated based on previous given

formulas:
W@;t = T

r = 14.105N. m
0.009525m = 1480.84N

WY;t = W@;t tanφ@ = 1480.84 ∗ tan 20.09 = 541.62N

W?;t = W@;t tan ψ = 1480.84 ∗ tan 45 = 1480.84N W = W@
cos ψ cosφC

= 1480.84
cos 14.5 cos 45 = 2163.12N

The forces between pinion 3 and gear 4 can be calculated based on previous given

formulas:
W@;t = T

r = 53.525N. m
0.0381m = 1404.86N

WY;t = W@;t tanφ@ = 1404.86 ∗ tan 20.09 = 513.83N

W?;t = W@;t tan ψ = 1404.86 ∗ tan 45 = 1404.86N W = W@
cos ψ cosφC

= 1404.86
cos 14.5 cos 45 = 2052.14N

## Stress Analysis

As this stage of the report, the size, torque, and other necessary information on performing

analysis of the gears are obtained. In order to analyze the gears, the bending stress, contact stress, Safety Factor and Wear Safety factor needs to be calculated. Using the provided equation

in the Shigley’s Mechanical Engineering design, the following equation is obtained in order to

calculate the bending stress in the gear:

- Wt is the tangential transmitted load. The value of the load is provided as seen in the

previous sections.

- KO is the overload factor of the gears. It can be found using the following table:

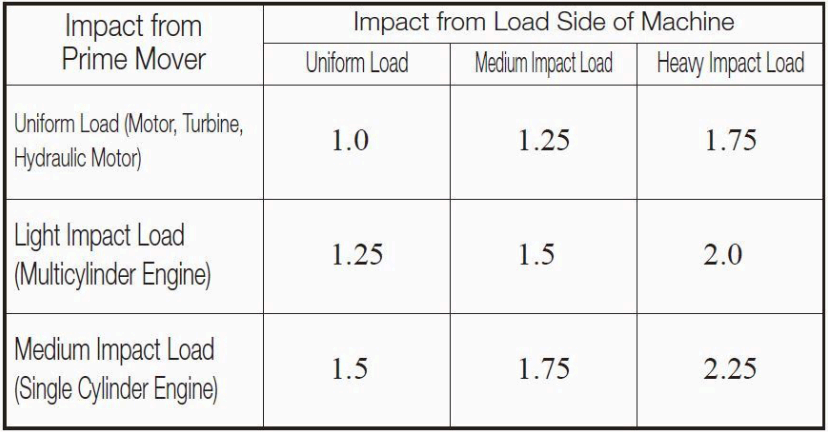
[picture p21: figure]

In the Boston Gear Catalog, the following table is also provided for reference for the

overload factor. (pg.66)

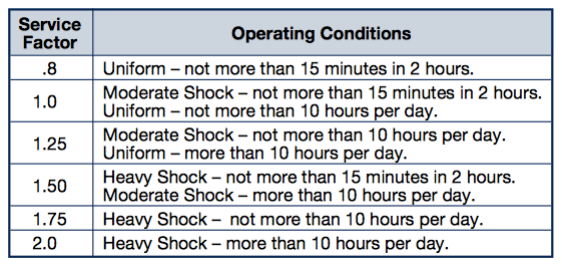
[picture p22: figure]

With a moderate shock and a uniform load, we can assume that the overload factor should

be 1.25.

- Kv , the Dynamic Factor of the gear is obtained as by assuming a quality number QV

of 5 as the gears are commercial-quality. Using the provided equations, the dynamic

factors are obtained,

- Ks The Size factor is obtained using the diametral pitch, face width and Lewis form

factor. As the normal pressure angle in our used gear is 14.5 degres, the following

table for the Lewis Factor is used:

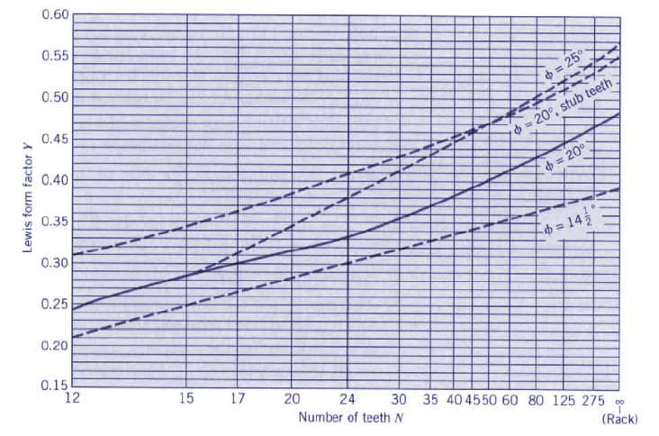
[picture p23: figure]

https://www.engineersedge.com/gears/lewis-factor.htm

- Km if the load distribution factor. Our gear is uncrowned, so Cmc = 1. With

S1/S<0.173, Cpm=1. Cma is calculated with the condition of commercial and enclosed

units. And Ce is neither for gearing adjusted at assembly or compatibility improved by

lapping, so ce=0.8. Using this the provided value, Km can be solved.

- The Rim-thickness factor is 1 as mB is greater than 1.2 .
- Although it would be difficult to find a datasheet for our gear, using this table:

https://eclass.upatras.gr/modules/document/file.php/MECH1178/18.%20Μετωπικοί%

20οδοντωτοί%20τροχοί/AGMA-908-B89.pdf , the approximate value for the bending-strength geometry factor is 0.364.

- Since we are using steel for the gear and pinion, the elastic coefficient is 2300 as in

described in the book.

- The surface condition factor Cf is 1 for our gear as the gears are steel-heardened and

polished.

- The geometry Factor I of the gear is obtained through the described equation in the

Shigley’s.

Using the numbers above, the bending stress and contact stress of the gears can be calculated.

Next, the factor of safety is calculated. The factor of safety of tooth bending is given in the

book.

- The formula of allowable bending stress is given in figure 14-2 in Shigley’s.

Assuming a Brinell hardness of 321, the allowable bending stress is obtained as

49,142.

- Stress Cycle Factors YN and ZN can be obtained through Figure 14-14 and Figure 14-

15 by using the calculated value of cycles.

- The reliability factor is assumed to be 1 with reliability of 99%
- The temperature factor is unity as the operational temperature would be below 120

degree Celsius.
Hardness-Ratio Factor CH is 1 as the gear use same material and would have a ratio for pinion and gear Brinell hardness below 1.2.
Bending Stress | 42209 | 40015 | 34607 | 33254
Contact Stress | 167743 | 94295 | 151888 | 85960
Bending FOS | 1.0 | 1.10 | 1.27 | 1.40
Contact FOS | 0.75 | 1.38 | 1.1 | 1.55

Stress calculation is presented in both Matlab and Excel files. Excel file include all 4 gears calculations, Matlab file includes gear 1 and 2 calculations.

## Discussion

Based on the stress calculation, the pinion gear attached on the motor shaft cannot withstand the contact stress with the required duty cycle. All other gears can fully meet the requirements. The failing pinion gear is iterated to meet the requirement. The failing pinion gear and its pair is changed to 8 transverse diametral pitch gear. Everything else remain. After the iteration, the pinion gear installed on the motor shaft can fully meet the requirement.

## Appendix A- 2D Assembly Drawing For Gear, Box and Gearbox

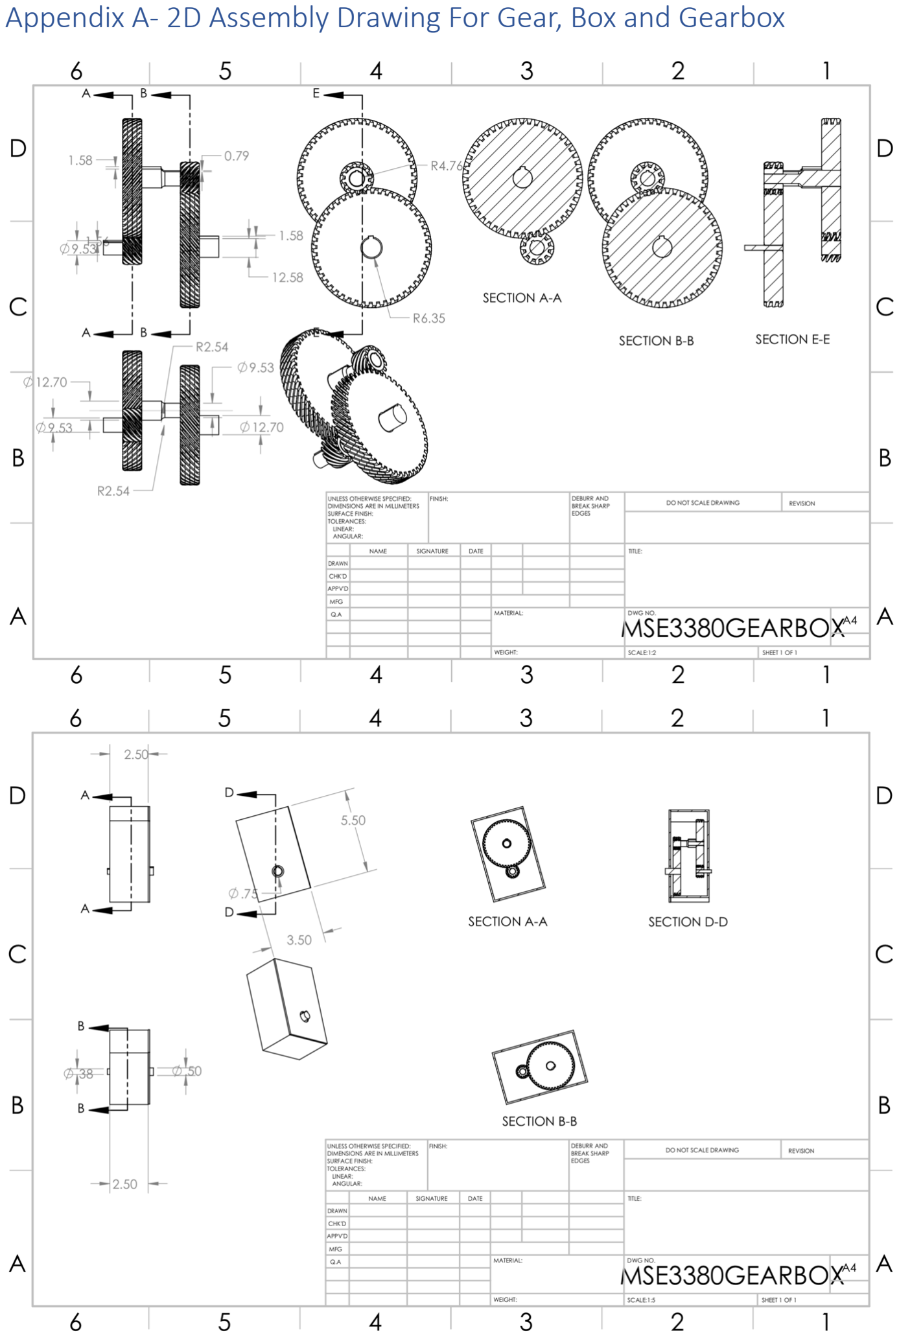
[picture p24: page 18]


## Citation

ASM Aerospace Specification Metals Inc., “AISI 4340 Steel, normalized, 100 mm (4 in.) round”, [Online]. Available: http://asm.matweb.com/search/SpecificMaterial.asp?bassnum=m434ae. [Accessed March 21, 2019]

EngineersEdge.com, “Lewis Factor Equation and Calculation for Gear Tooth”, 2019. [Online]. Available: https://www.engineersedge.com/gears/lewis-factor.htm. [Accessed March 21, 2019]

R. G. Budynas, and J. K. Nisbett, Shigley’s Mechanical Engineering Design, 10th edition. New York, NY: McGraw Hill Education, 2014.

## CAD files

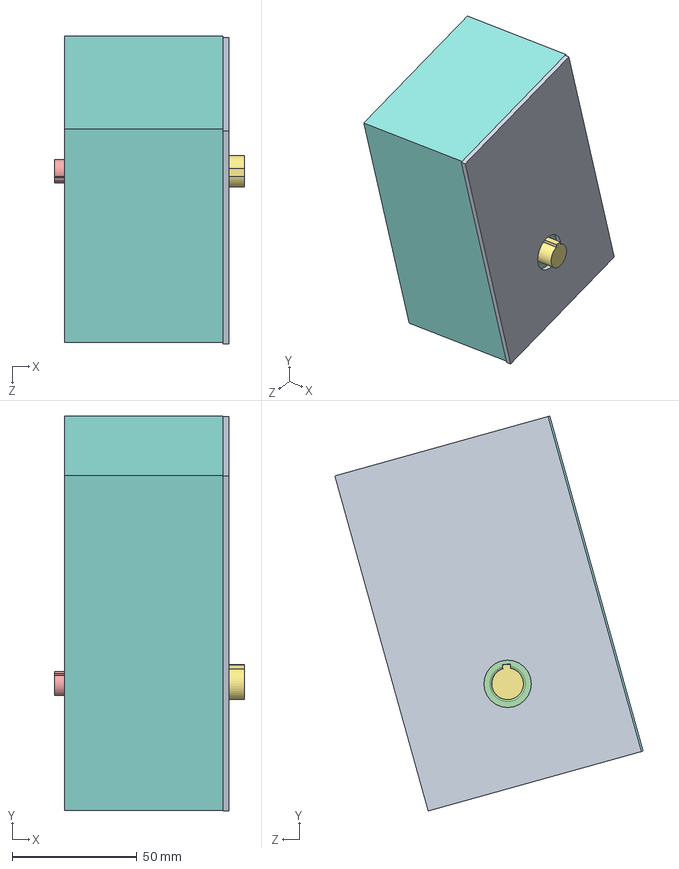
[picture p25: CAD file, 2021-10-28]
Interm/MSE3380GROUP5INTERIMSLWK/MSE3380GEARBOX.SLDASM
76.3 x 158.6 x 123.9 mm
H1612L
H1612R
H1648L
H1648R
Shaft1
Shaft2
Shaft3
gearbox
gearboxcover

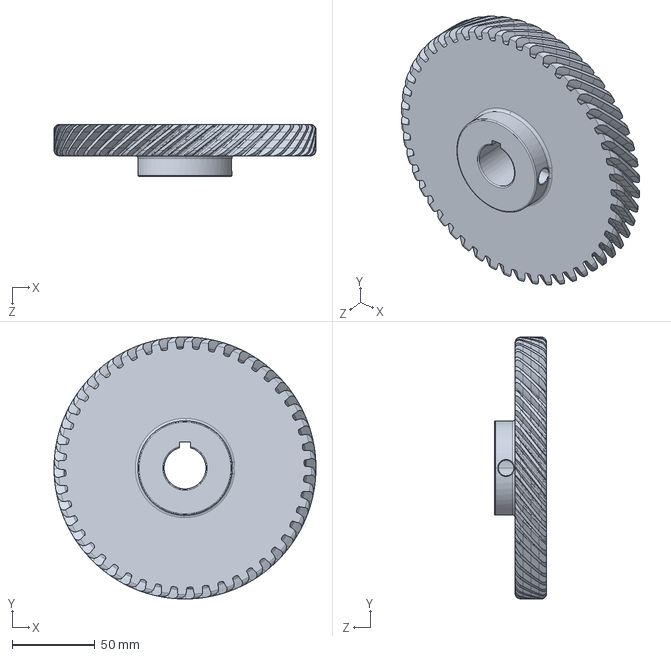
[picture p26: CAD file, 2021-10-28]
Final/MSE3380SolidworksFiles/HS848R.SLDPRT
158.8 x 158.7 x 31.7 mm

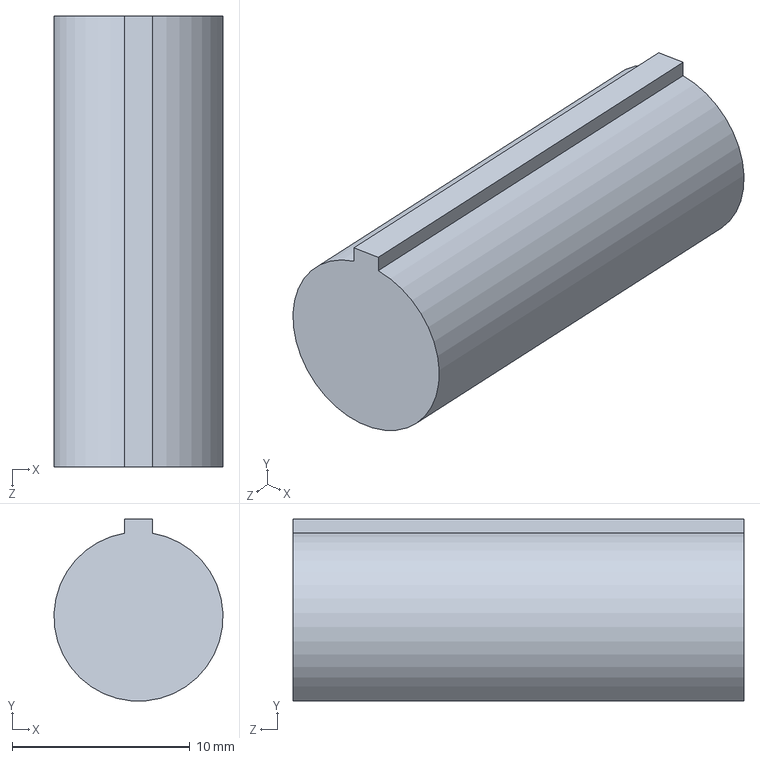
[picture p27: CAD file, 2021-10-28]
Interm/MSE3380GROUP5INTERIMSLWK/Shaft1.SLDPRT
9.52 x 10.2 x 25.4 mm

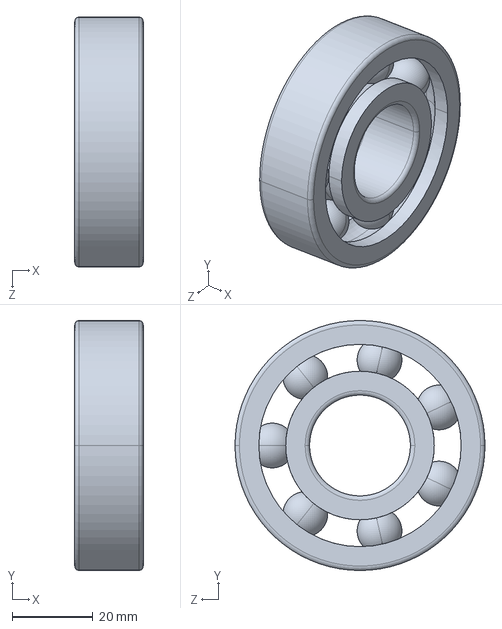
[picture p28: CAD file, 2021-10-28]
Final/MSE3380SolidworksFiles/305K.SLDPRT
17.0 x 62.0 x 62.0 mm

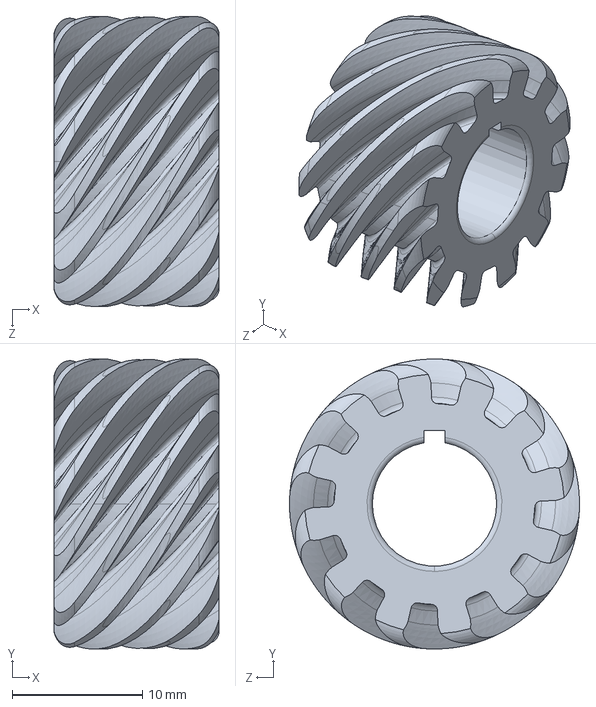
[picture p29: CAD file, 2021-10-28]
Interm/MSE3380GROUP5INTERIMSLWK/H1612L.SLDPRT
12.6 x 22.2 x 22.2 mm

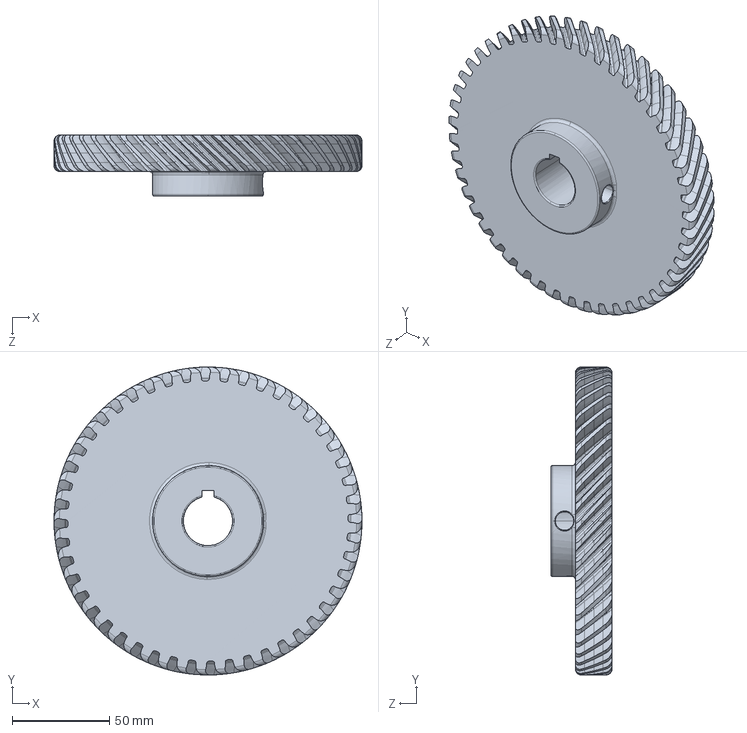
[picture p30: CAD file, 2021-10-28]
Final/MSE3380SolidworksFiles/HS848L.SLDPRT
158.8 x 158.7 x 31.7 mm

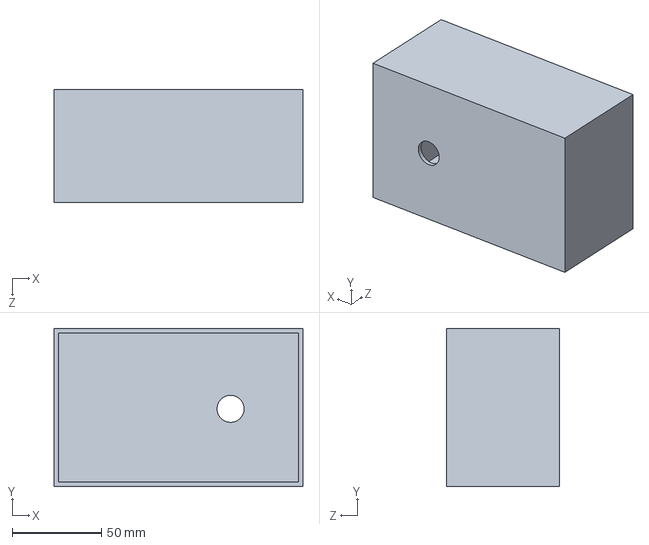
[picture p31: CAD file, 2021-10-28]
Interm/MSE3380GROUP5INTERIMSLWK/gearbox.SLDPRT
139.7 x 88.9 x 63.5 mm

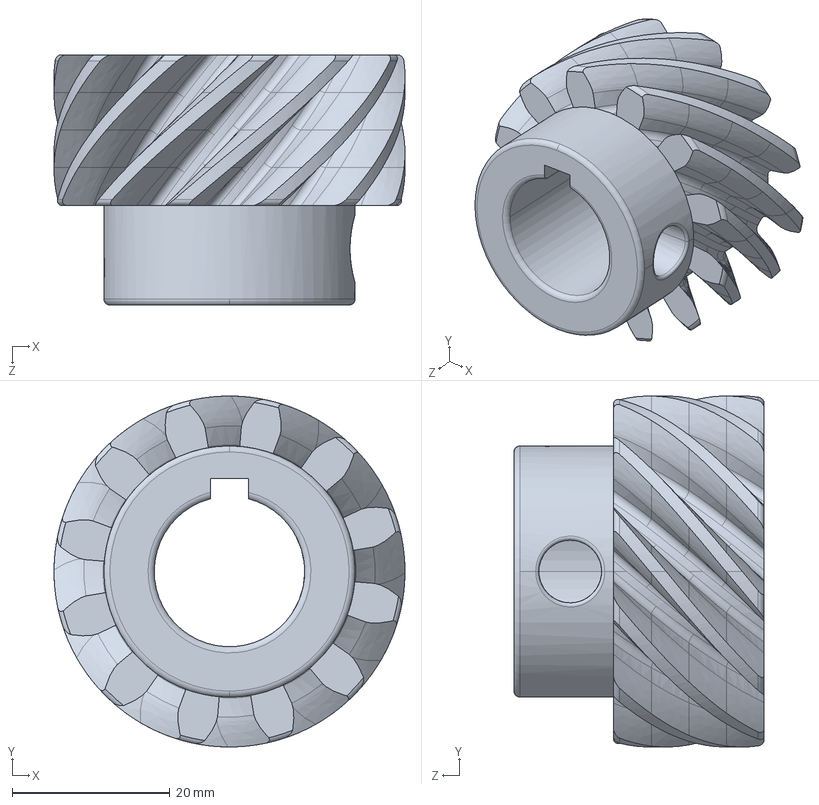
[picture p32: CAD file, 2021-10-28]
Final/MSE3380SolidworksFiles/HS812R.SLDPRT
44.5 x 44.4 x 31.7 mm

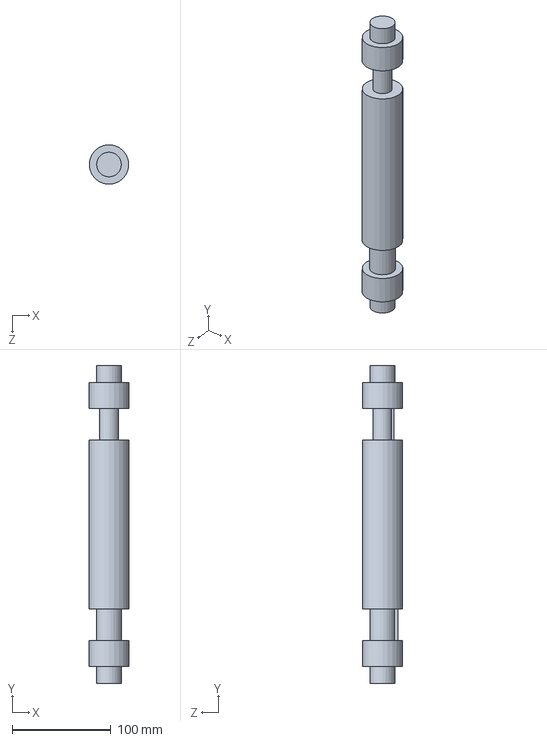
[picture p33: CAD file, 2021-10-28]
Final/MSE3380SolidworksFiles/IntermediateShaft.SLDPRT
40.0 x 321.8 x 40.0 mm

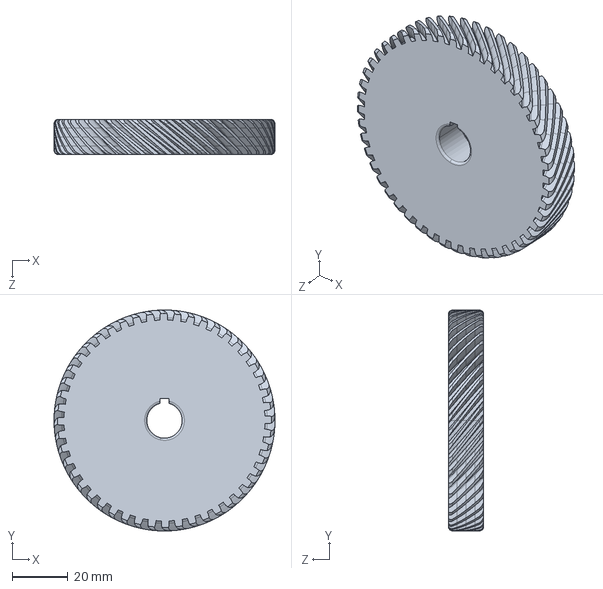
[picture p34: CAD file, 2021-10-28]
Interm/MSE3380GROUP5INTERIMSLWK/H1648L.SLDPRT
79.4 x 79.4 x 12.6 mm

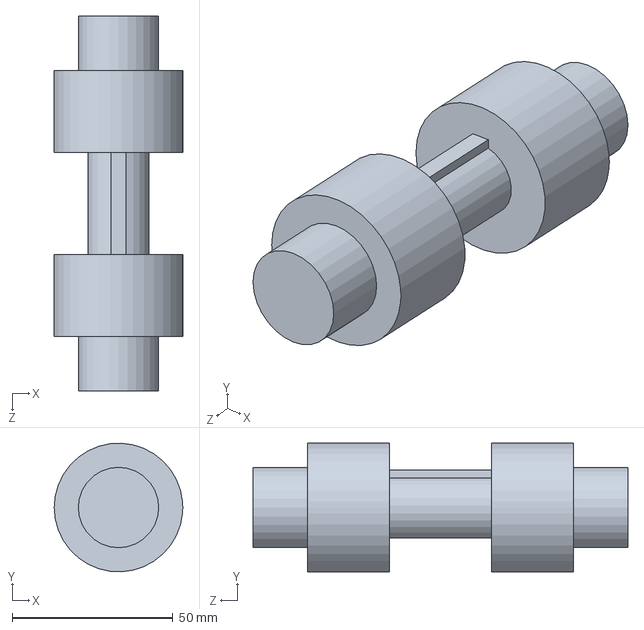
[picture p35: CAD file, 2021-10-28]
Final/MSE3380SolidworksFiles/InputShaft.SLDPRT
40.0 x 40.0 x 116.6 mm

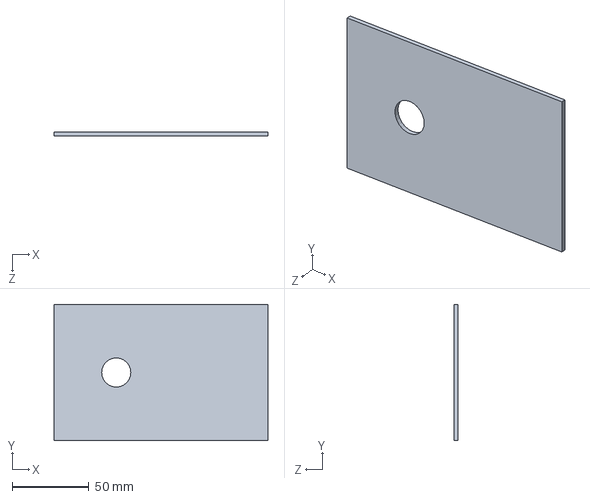
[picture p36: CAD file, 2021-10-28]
Interm/MSE3380GROUP5INTERIMSLWK/gearboxcover.SLDPRT
139.7 x 88.9 x 2.54 mm

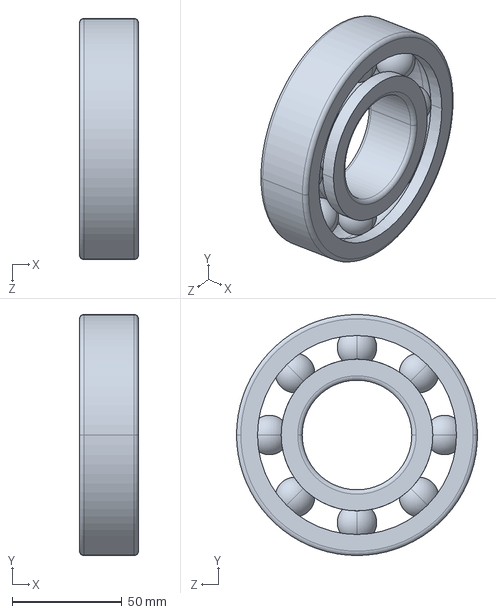
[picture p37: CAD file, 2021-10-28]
Final/MSE3380SolidworksFiles/310K.SLDPRT
27.0 x 110.0 x 110.0 mm

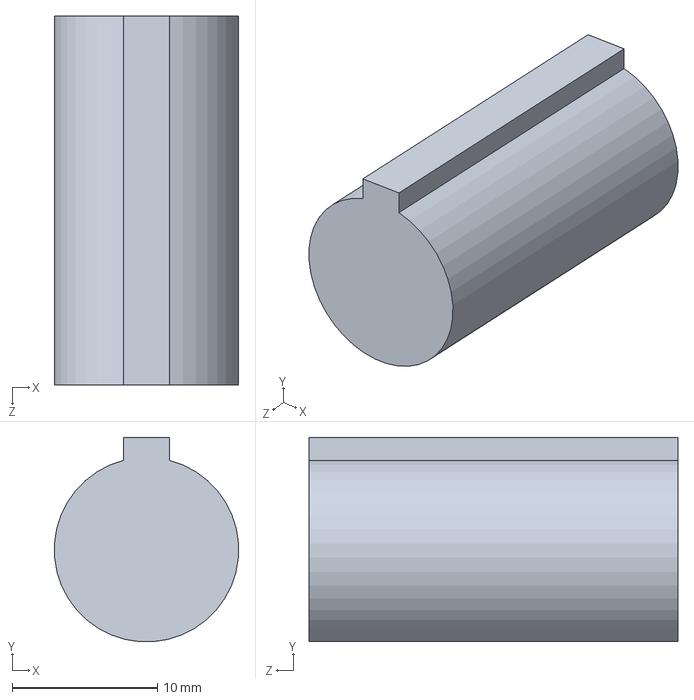
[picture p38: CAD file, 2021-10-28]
Interm/MSE3380GROUP5INTERIMSLWK/Shaft3.SLDPRT
12.7 x 14.1 x 25.4 mm

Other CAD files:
Interm/MSE3380GROUP5INTERIMSLWK/H1612R.SLDPRT
Final/MSE3380SolidworksFiles/OutputShaft.SLDPRT
Interm/MSE3380GROUP5INTERIMSLWK/H1648R.SLDPRT
Final/MSE3380SolidworksFiles/HS812L.SLDPRT
Final/MSE3380SolidworksFiles/308K.SLDPRT
Interm/MSE3380GROUP5INTERIMSLWK/Shaft2.SLDPRT
